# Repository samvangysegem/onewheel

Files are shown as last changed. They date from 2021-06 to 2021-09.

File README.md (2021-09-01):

## OneDuino
&nbsp;
&nbsp;
&nbsp;
&nbsp;
&nbsp;
&nbsp;

### :clipboard: Summary
The goal of this project is to build a one-wheeled robot from scratch. This includes mechanical design of the robot, component selection, electrical design, control system design and embedded programming. The MCU at the hearth of the robot is a Teensy 4.0, packing enough computational power to experiment with optimisation based control strategies. I started this project with two goals in mind: rehearsing a number of important aspects of control theory and the Arduino C/C++ languages and generally improving my embedded programming skills. 

### :construction: Progress
- [x] Model derivation using Euler-Lagrange equations
- [x] 3D design of robot in Solidworks
- [x] Component selection
- [x] LQR control system design
- [x] Circuit design
- [x] 3D printing parts and assembly
- [ ] Coding
- [ ] Countless hours of debugging untill this thing will work

### :computer: Simulation results
This simulation serves as a validation of the correct operation of the LQR controller. The simulation starts with an initial disturbance and ends in a balanced state in x = 1. The LQR control is evidently based on the linearised version of the state-space equations and calculates the optimal input for an infinite optimisation horizon. The simulation on the other hand is the result of numerically integrating the original nonlinear state space equations using a fourth-order Runge-Kutta method.

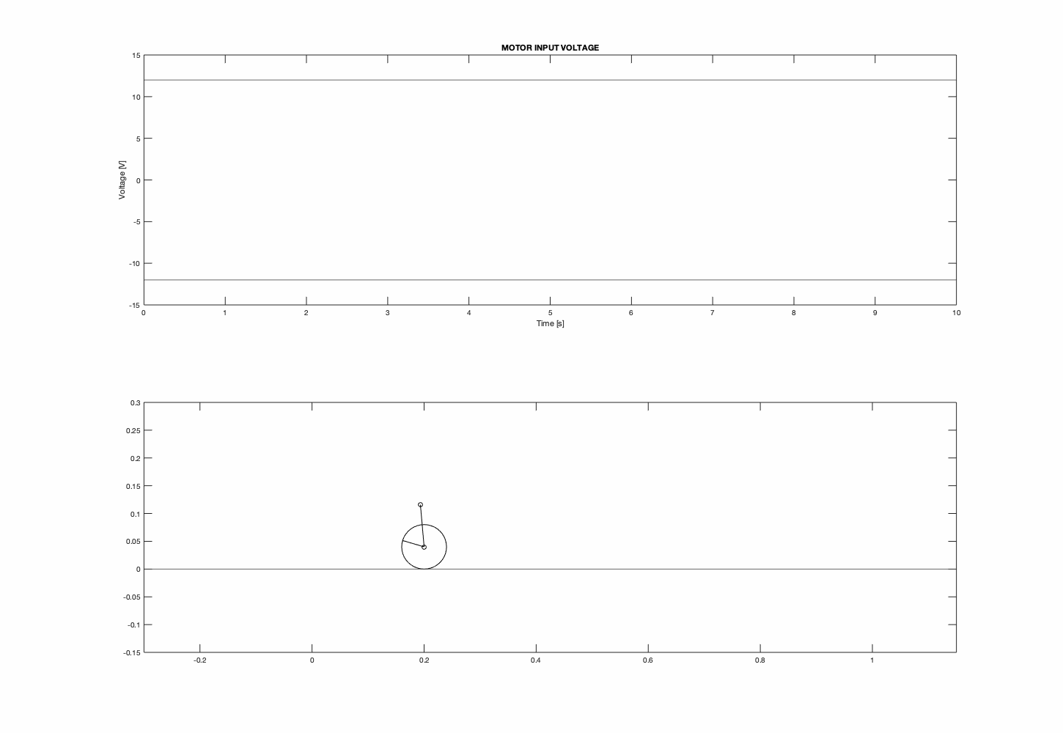
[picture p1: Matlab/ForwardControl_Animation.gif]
Forward LQR Control

 
### :battery: Circuit Design
**Mk1**
The circuit is built on a prototyping PCB given the low complexity of the circuit, which wasn't worth the long waiting time when ordering PCBs online. The board features female headers for connecting the Teensy 4.0 and interfacing with all its pins, 2 male header rows for driving the motors and interfacing with their respective encoders and an MPU6050 module. The red-black wires connect to the Cytron MDD3A dual channel DC motor driver board, in addition to a number of male-female headers for control. As the main focus of this project isn't brushed DC motor control, I didn't bother designing the H-bridges and corresponding driving circuits myself (an idea for an upcoming project, albeit a bit more challenging by replacing the brushed DC motors with brushless DC motors).

| PCB Front | PCB Back |
| --- | --- |
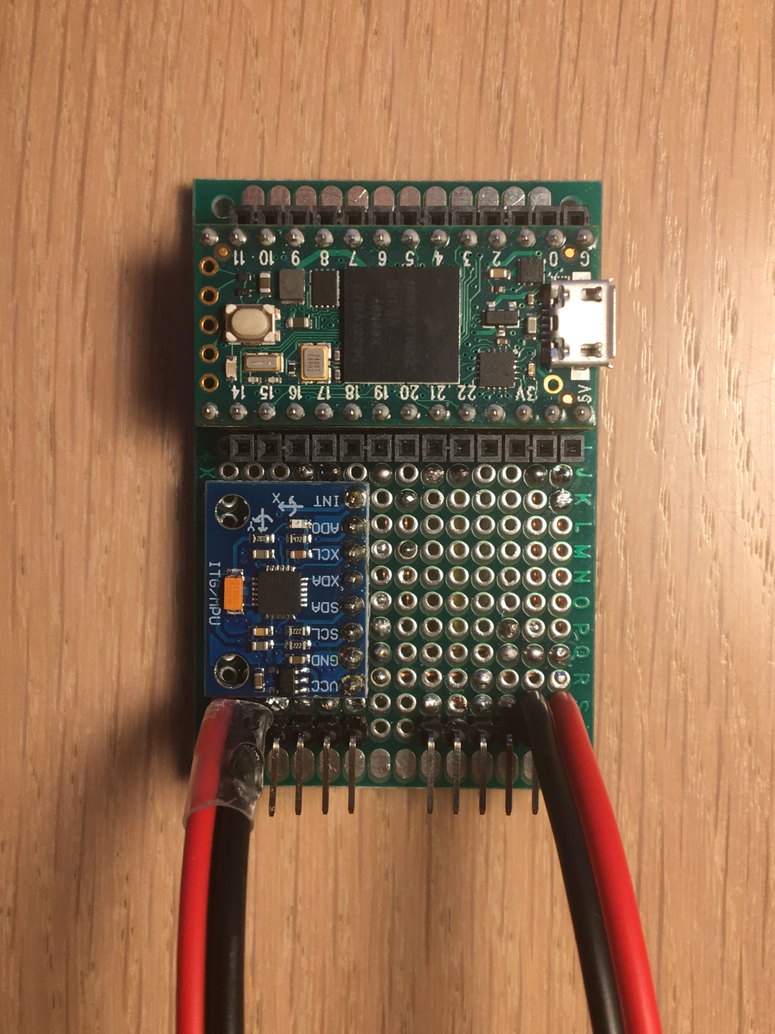
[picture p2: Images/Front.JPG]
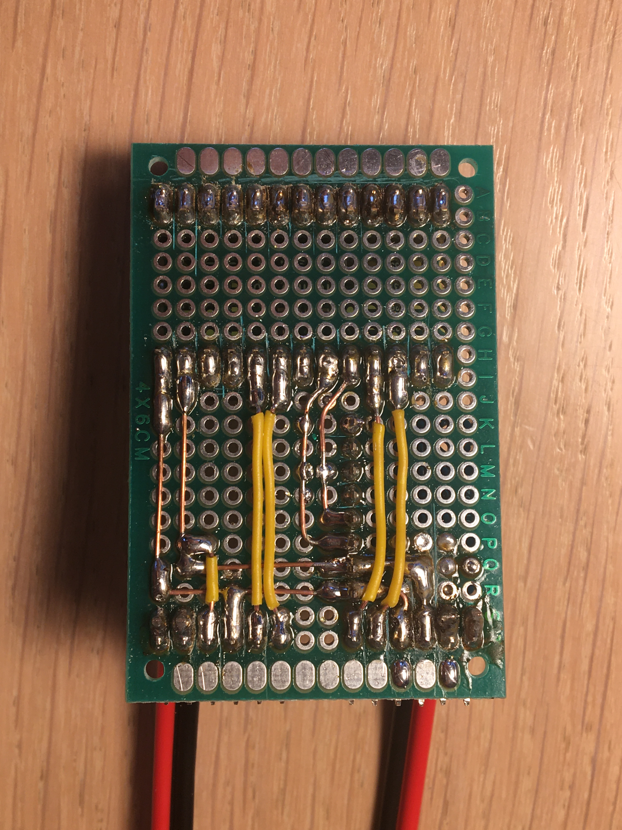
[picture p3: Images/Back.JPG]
 | 

**Mk2**
Since the first design immediately burned down upon testing, as described in the Troubleshooting section below, a second design of the prototyping PCB was made with some changes mitigating the risk of short circuits. The main difference in design is the use of both sides of the prototyping PCB and more careful soldering, not burning the isolation of important wires...

| PCB Front | PCB Back |
| --- | --- |
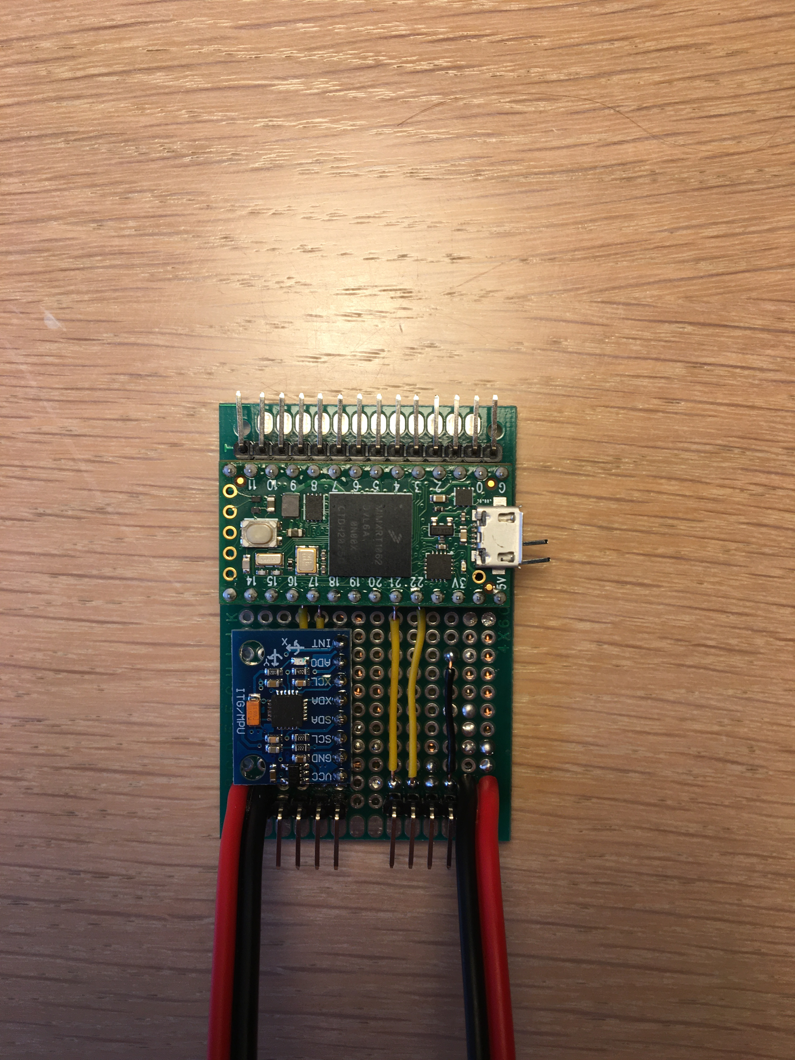
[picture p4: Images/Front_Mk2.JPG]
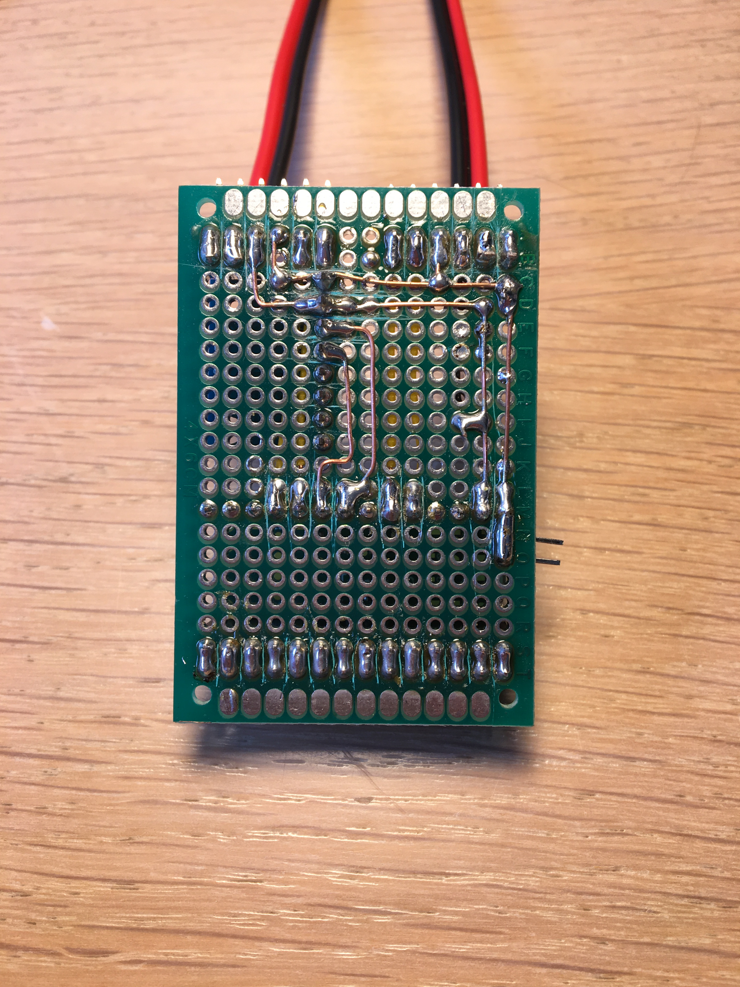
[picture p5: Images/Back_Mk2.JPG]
 | 

### :hammer_and_wrench: Assembly
A few hours of "being creative with incorrect dimensioning of bearing clearances and shaft diameters" later, the full assembly is finished (except for the belt, which is still on its way but we can imagine that part). No short circuits, not falling apart and it looks pretty sweet even if I say so myself...

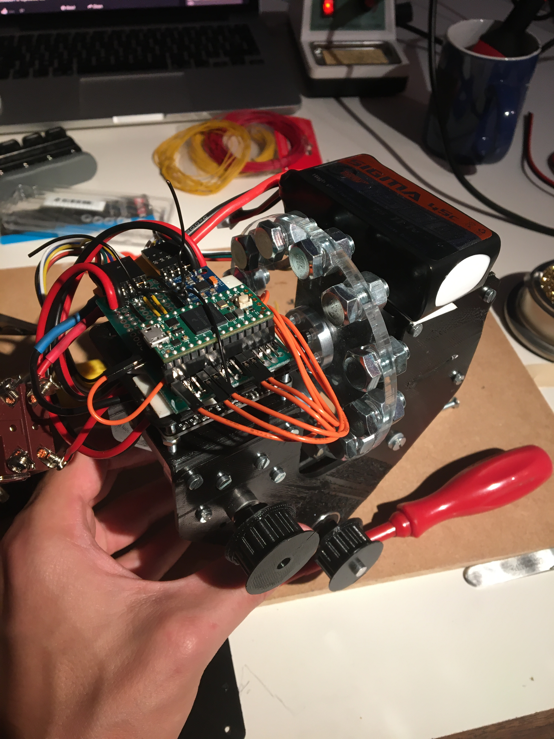
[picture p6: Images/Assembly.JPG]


### :warning: Troubleshooting
- Short circuit occured on the prototyping PCB during a motor test with battery supply. Upon closer inspection, the isolation of one of the motor wires melted during soldering. Solder from a wire next to it entered the isolation through this hole, nearly making contact with the other wire. Even though no short circuit was measured during testing, the higher current required for driving the motor in combination with slight wire movement (possibly) caused a short circuit between these two wires. As a result, a voltage of 12 V was applied to the GND output of the Teensy, resulting in a fried voltage regulator, IMU (also connected to this GND) in addition to internal damage of the Teensy.

    **Conclusion** 
    - When wire isolation melted and unsure whether a short circuit will occur, assume the worst
    - Test motor interfaces first, without Teensy

- LQR control currently is way to aggressive. The robot kinda wants to destroy itself upon receiving power and starting in "balance". There are two ways to address this problem (in my opinion):
    - Improve the model of the balancer
    - Increase the cost of the applied input

    The latter one earns my preference since it requires less rework to the model and code. The influence of these changes will first be verified in simulation before applying it to the actual model.

    **Update** 
    Upon further testing, the problem couldn't be solved as easily as described above. In order to debug this matter in a qualitative manner, following actions are required:
     - Write a python script responsible for visualising and debugging the data sent via the serial interface
     - Design filters for the measured data
     - Debug the Kalman filter class

    Additionally, some library files were added into the project folder itself as I changed some of the parameters of the MPU6050 in those libraries and this was the only way for the Arduino IDE to use the correct libraries.

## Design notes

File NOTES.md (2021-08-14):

## General structure

https://docs.wpilib.org/en/stable/docs/software/commandbased/what-is-command-based.html

## Mechanical Design

### Flywheel Design
3D printed wheel lacks the weight to fulfill the role of a flywheel. Therefore, a number of bolts are added at a large outside diameter to increase the total moment of inertia.

Source: https://itafasteners.com/weight-chart.php
According to the site mentioned above, the total weight of 100 M8 bolts is approximately 1.593kg, resulting in a weight of 15.9g x 12 at a radius of 40mm (with nuts).

Outside diameter: 95mm
Inside diameter: 7mm
Diameter of bols: 80mm
Pitch diameter fastening nuts: 19.06mm
Diameter fastening nuts: 3.4mm

**Components**
* Bolts
    * Online store: https://nl.rs-online.com/web/p/hex-bolts/0190254
* Nuts
    * Online store: https://nl.rs-online.com/web/p/hex-nuts/1224404

### Belt/Pulley Design
Calculator: https://www.bbman.com/belt-length-calculator/

* Center distance
    * 70 mm

**Components**
* Pulleys
    * 16 teeth
    * 25.5 mm pitch diameter
    * 3D Model: https://www.traceparts.com/en/product/gates-standard-pulley-t5-pitch-5-mm-width-10-mm-number-of-teeth-16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

* Belt: 220mm length
    * Online store: https://nl.rs-online.com/web/p/timing-belts/4745347/

## Software Design
Control is split up in forwards and sideways control, assuming independent systems (which off course is not correct but for sufficiently small deviations should provide a good approach to control). 

### MPU6050
Calibration is required to guarantee correct operating behaviour. This can be achieved through the MPU 6050 library in the Arduino IDE, example sketch "IMU_Zero.ino". Calibration is best performed before installing the sensor on the robot in order to yield optimal results on a flat surface.

General operation: https://mjwhite8119.github.io/Robots/mpu6050

### Motor Encoders

### Kalman Filter
The Kalman filter is responsible for estimating the necessary velocity estimates based on the position estimates and mathematical model. Immediately deriving the velocity from the position estimate would induces a high amount of noise in the velocity estimates. Integrating the acceleration values on the other hand would be another good approach, however these are quite difficult to access.

### LQR Control

### Matrix4 and Vector4
Custom classes written to perform matrix calculations for Kalman filter and LQR control. Row and column vectors are separated in order to easily implement the multiplication overloading of these different vectors with each other and matrices.
- [ ] Inverse operator for Matrix class (efficient implementation)
- [ ] Copy constructors

## Git Commands
git status
git log --stat
git add
git commit -m "Message"
git push
git pull
git rm --cached *filename*

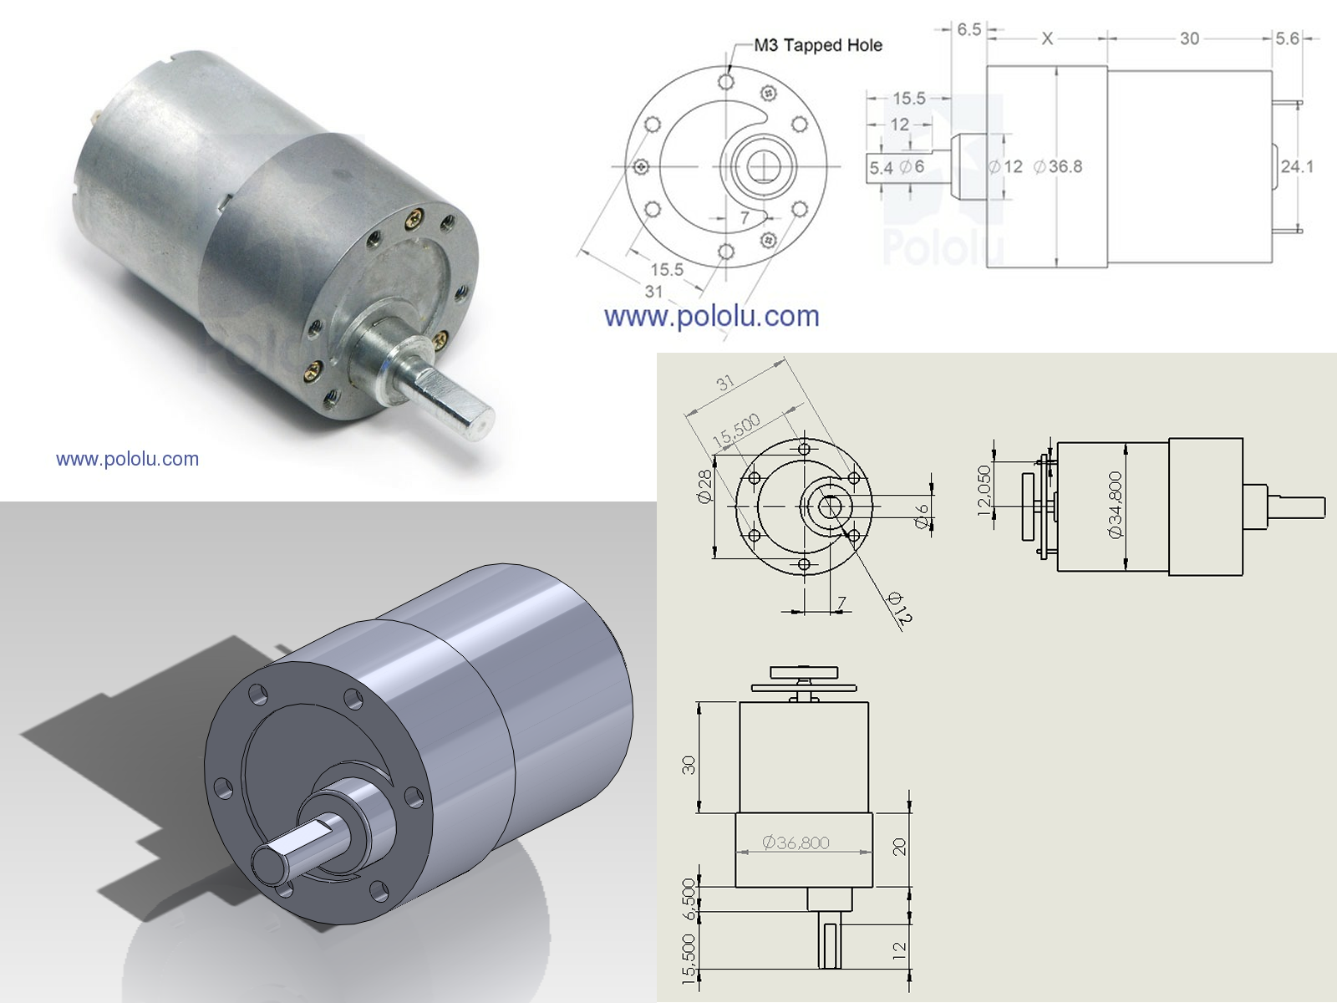
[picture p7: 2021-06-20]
Solidworks/pololu-37dx52l-mm-with-64-cpr-encoder/Renderings/pololu-37D-encoder.png

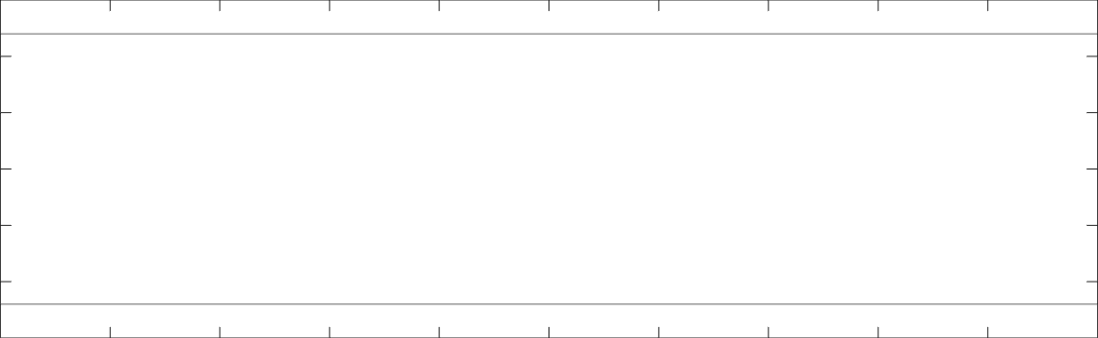
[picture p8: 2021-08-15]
Matlab/ForwardControl_Control.gif

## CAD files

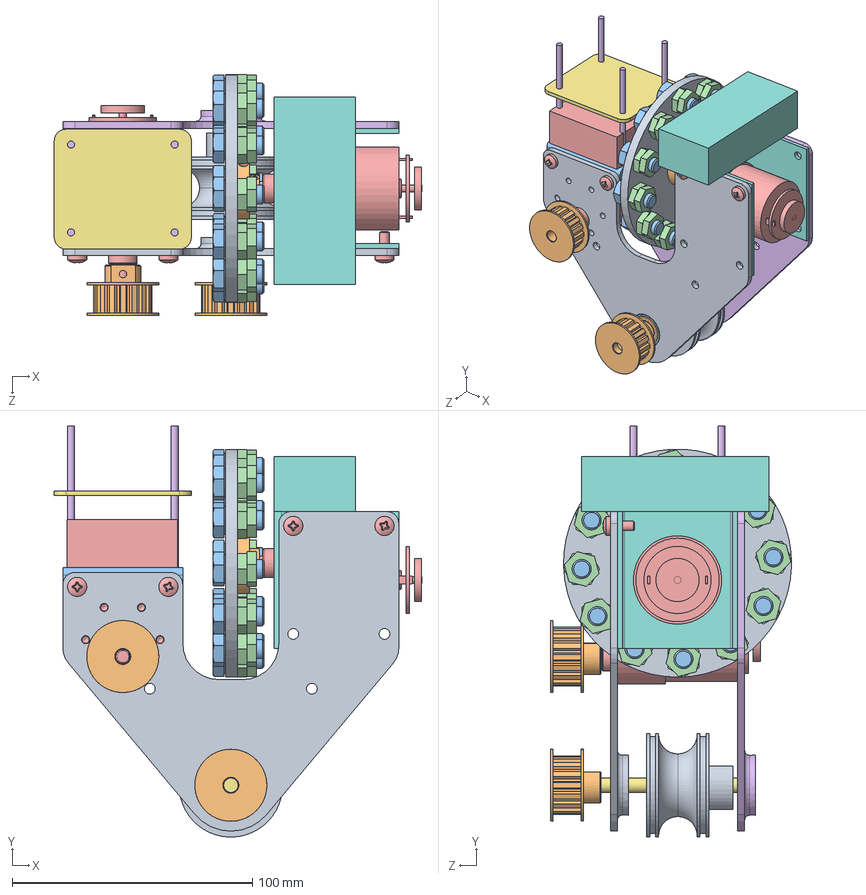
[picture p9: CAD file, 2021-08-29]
Solidworks/OneWheel.SLDASM
153.1 x 171.2 x 100.4 mm
ZijplaatL
_626_2Z_PART1_2 x 2
_626_2Z_PART2_4 x 2
_626_2Z_PART3_6 x 16
pololu-37D-encoder x 2
ZijplaatR
Wheelaxis
Motorhouder
Vliegwiel
Wheel Hub
Elechouder
NUTM4 x 2
din_en_iso7045_m4x10_4_8h x 4
Elecsupportbeam x 4
Elecmount
Battery
Velg
T5Pulley2 x 2
screw_din_933-m8x16-10_9-a x 12
fath_4din439bm8e x 24
Contra

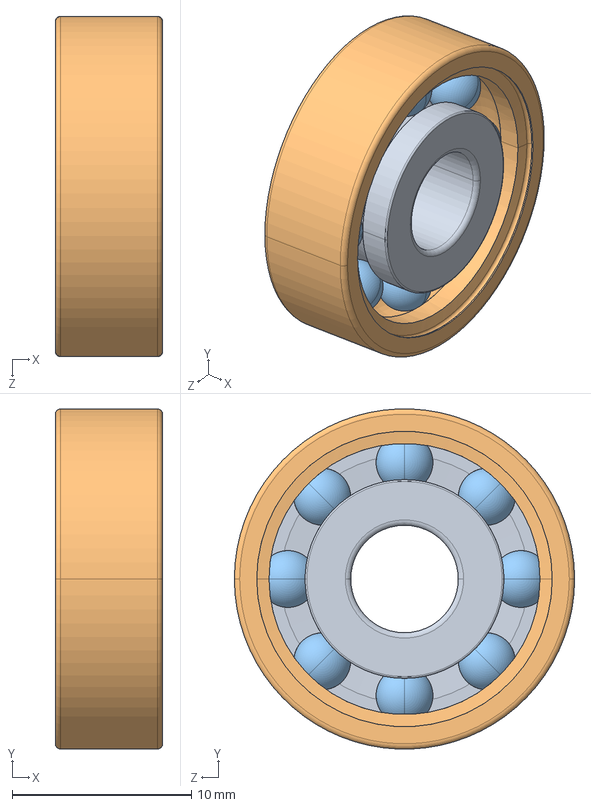
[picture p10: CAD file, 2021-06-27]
Solidworks/626_2Z.sldasm
6.00 x 19.0 x 19.0 mm
_626_2Z_PART1_2
_626_2Z_PART2_4
_626_2Z_PART3_6 x 8

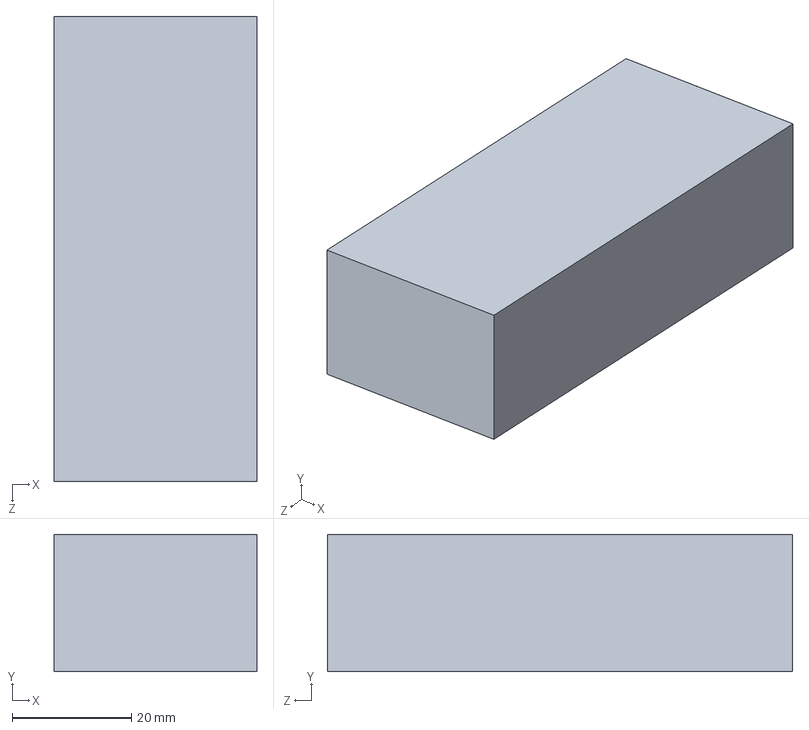
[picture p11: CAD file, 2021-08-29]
Solidworks/Battery.SLDPRT
34.0 x 23.0 x 78.0 mm

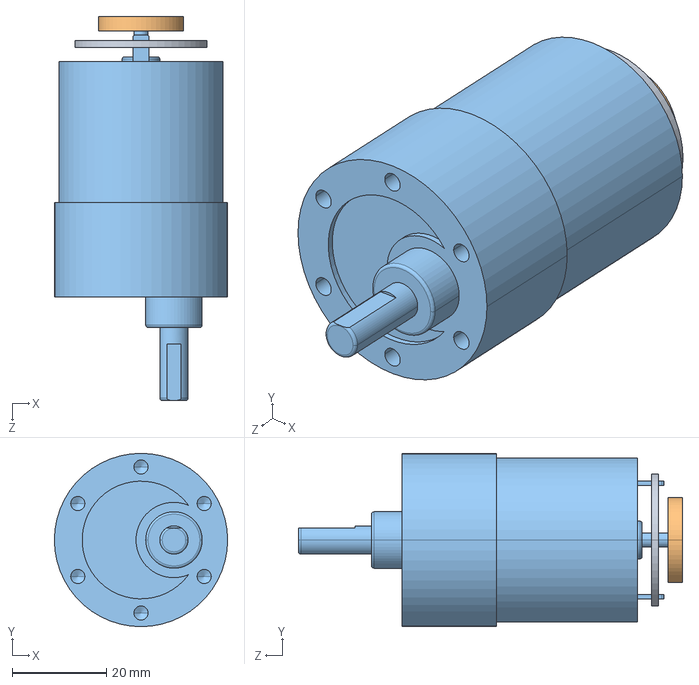
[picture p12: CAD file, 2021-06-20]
Solidworks/pololu-37dx52l-mm-with-64-cpr-encoder/pololu-37D-encoder.STEP
36.8 x 36.8 x 81.5 mm

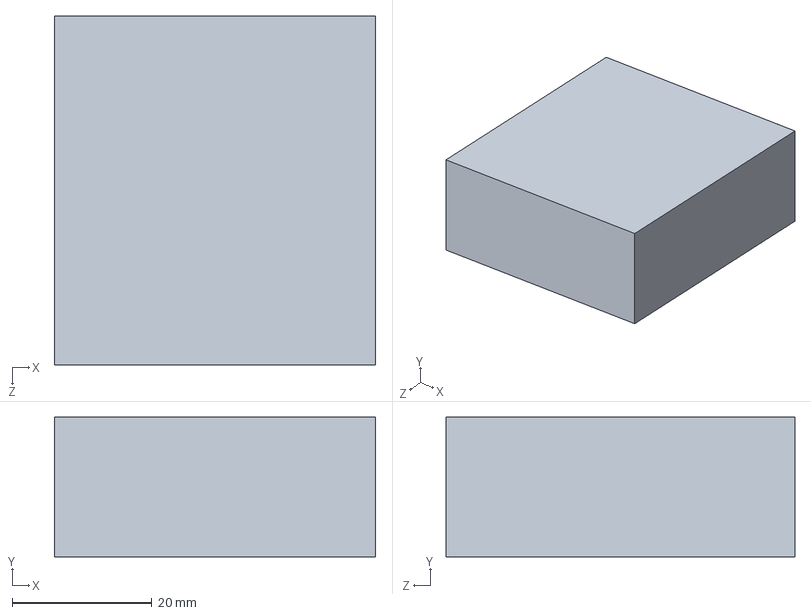
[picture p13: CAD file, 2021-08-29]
Solidworks/Contra.SLDPRT
46.0 x 20.0 x 50.0 mm

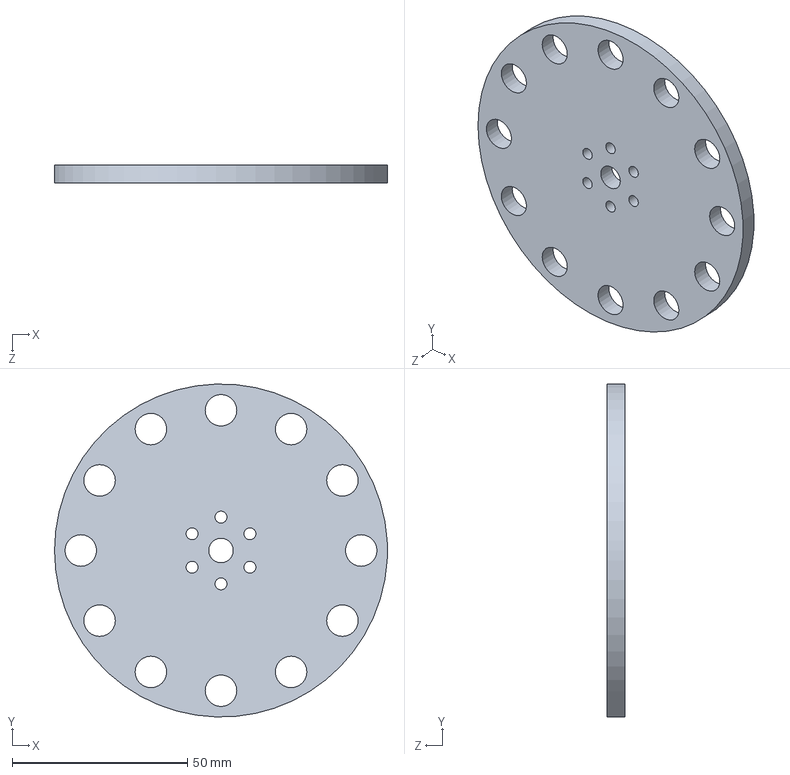
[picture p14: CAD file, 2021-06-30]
Solidworks/Vliegwiel.SLDPRT
95.0 x 95.0 x 5.00 mm

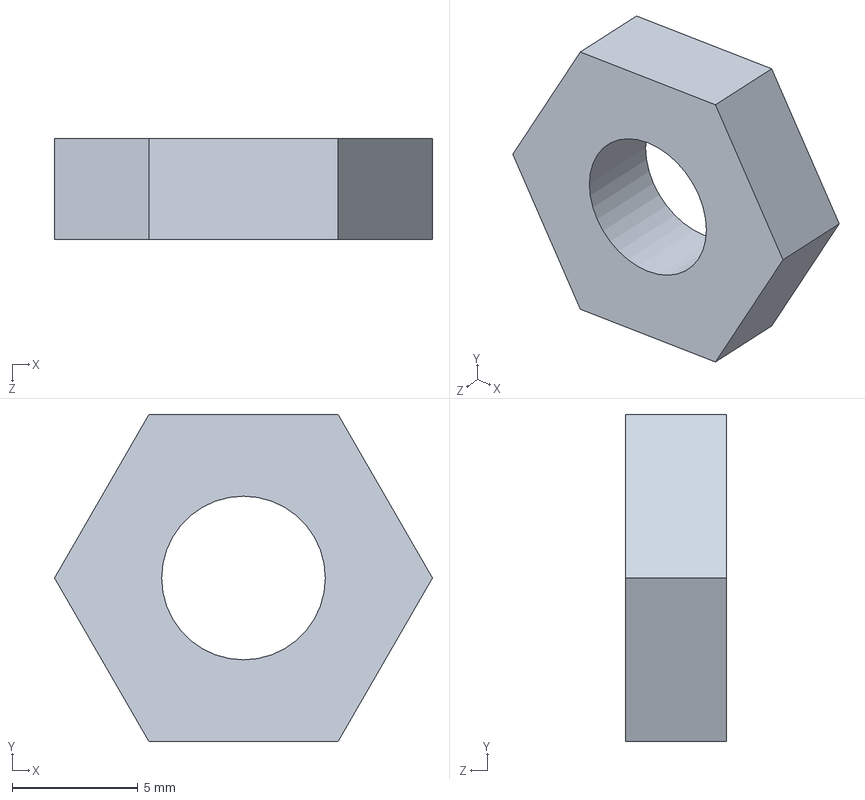
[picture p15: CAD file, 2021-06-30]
Solidworks/fath_4din439bm8e.SLDPRT
15.0 x 13.0 x 4.00 mm

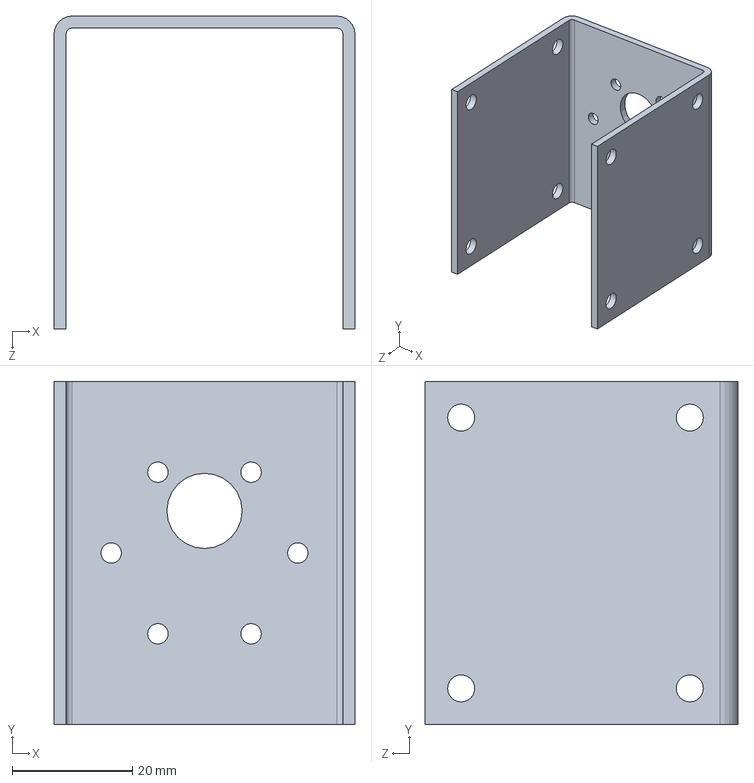
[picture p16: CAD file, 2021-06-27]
Solidworks/Motorhouder.SLDPRT
50.0 x 57.0 x 52.0 mm

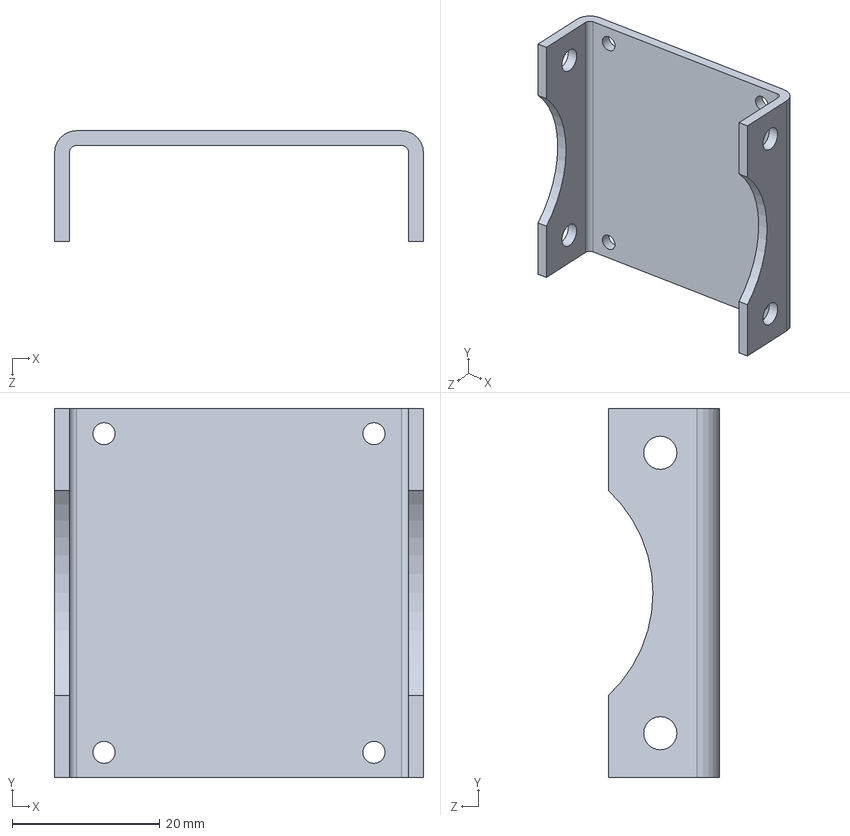
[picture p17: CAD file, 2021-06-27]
Solidworks/Elechouder.SLDPRT
50.0 x 50.0 x 15.0 mm

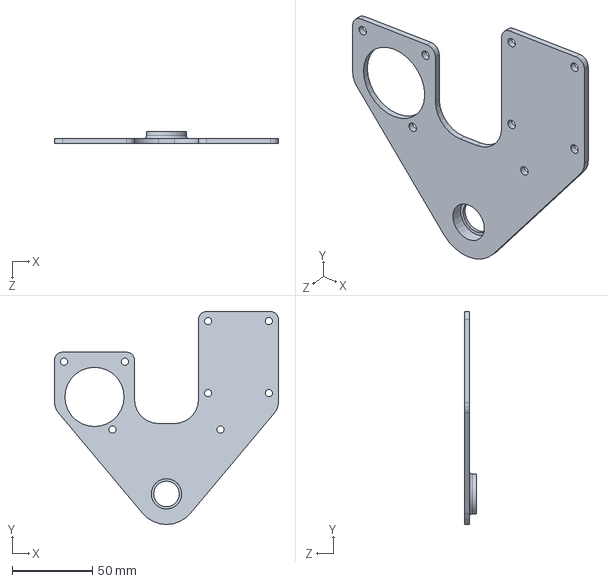
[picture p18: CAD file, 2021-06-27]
Solidworks/ZijplaatR.SLDPRT
140.0 x 133.1 x 7.50 mm

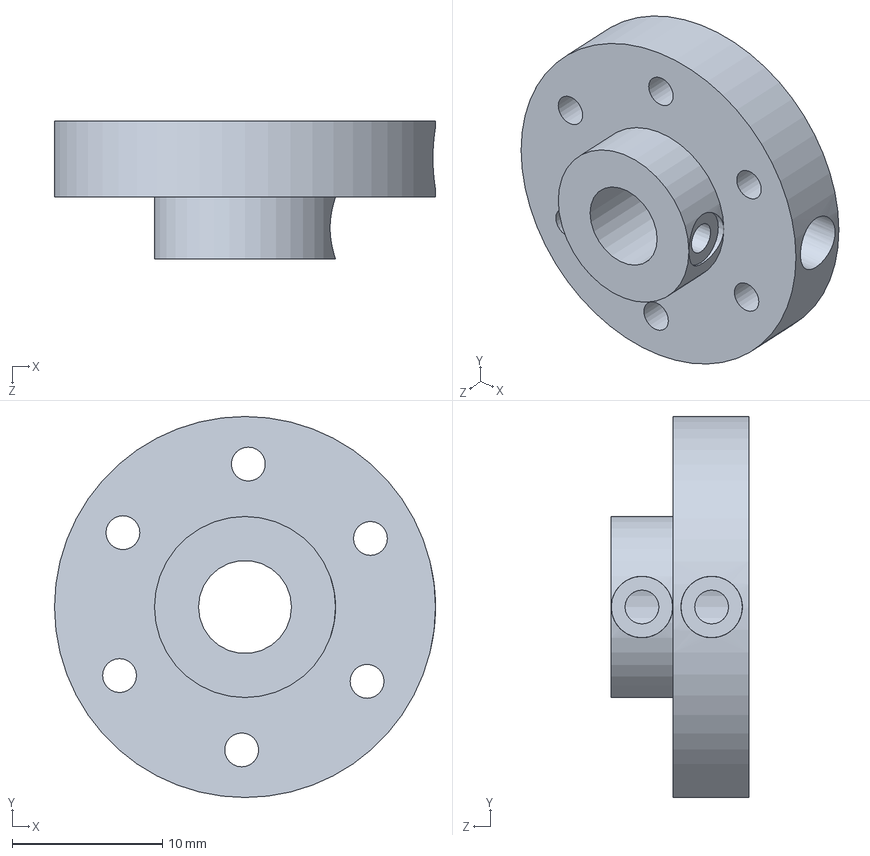
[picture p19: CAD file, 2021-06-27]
Solidworks/Wheel Hub.SLDPRT
25.4 x 25.4 x 9.21 mm

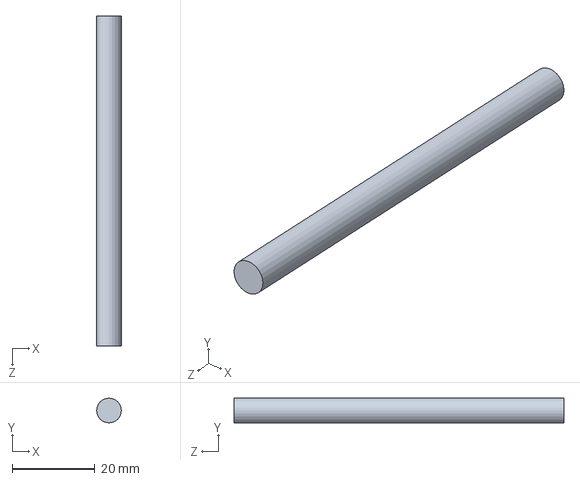
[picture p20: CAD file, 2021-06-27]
Solidworks/Wheelaxis.SLDPRT
6.00 x 6.00 x 80.0 mm

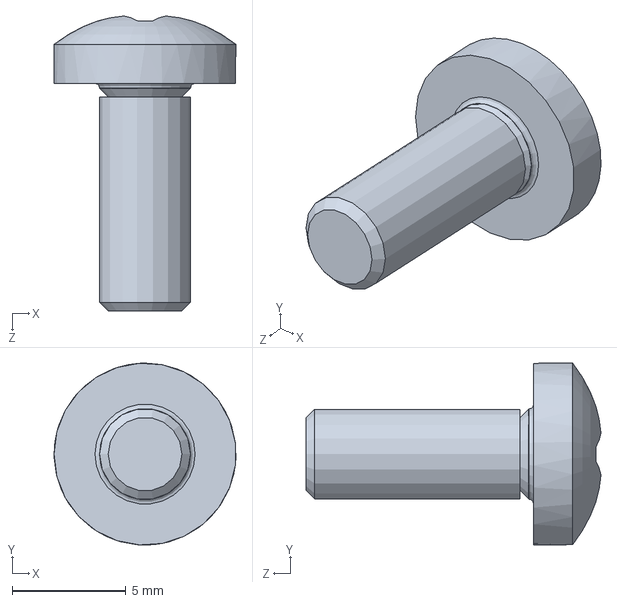
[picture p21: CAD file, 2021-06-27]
Solidworks/din_en_iso7045_m4x10_4_8h.SLDPRT
8.00 x 7.99 x 13.0 mm

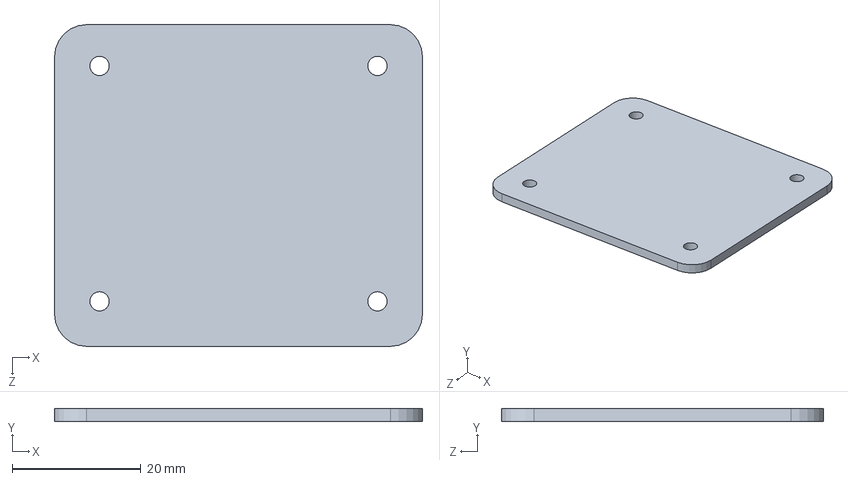
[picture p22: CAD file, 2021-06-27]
Solidworks/Elecmount.SLDPRT
57.2 x 2.00 x 50.0 mm

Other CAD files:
Solidworks/_626_2Z_PART3_6.sldprt
Solidworks/_626_2Z_PART2_4.sldprt
Solidworks/ZijplaatL.SLDPRT
Solidworks/NUTM4.SLDPRT
Solidworks/Elecsupportbeam.SLDPRT
Solidworks/MLXPulley.SLDPRT
Solidworks/PanHeadCrossRecessedScrew_M4x12.STEP
Solidworks/T5Pulley.SLDPRT
Solidworks/T5Pulley2.SLDPRT
Solidworks/Velg.SLDPRT
Solidworks/_626_2Z_PART1_2.sldprt
Solidworks/din_en_iso7045_m4x14_4_8h.SLDPRT
Solidworks/pololu-37dx52l-mm-with-64-cpr-encoder/pololu-37D-encoder.SLDDRW
Solidworks/pololu-37dx52l-mm-with-64-cpr-encoder/pololu-37D-encoder.SLDPRT
Solidworks/pololu-37dx52l-mm-with-64-cpr-encoder/pololu-37D-encoder.STL
Solidworks/screw_din_933-m8x16-10_9-a.SLDPRT

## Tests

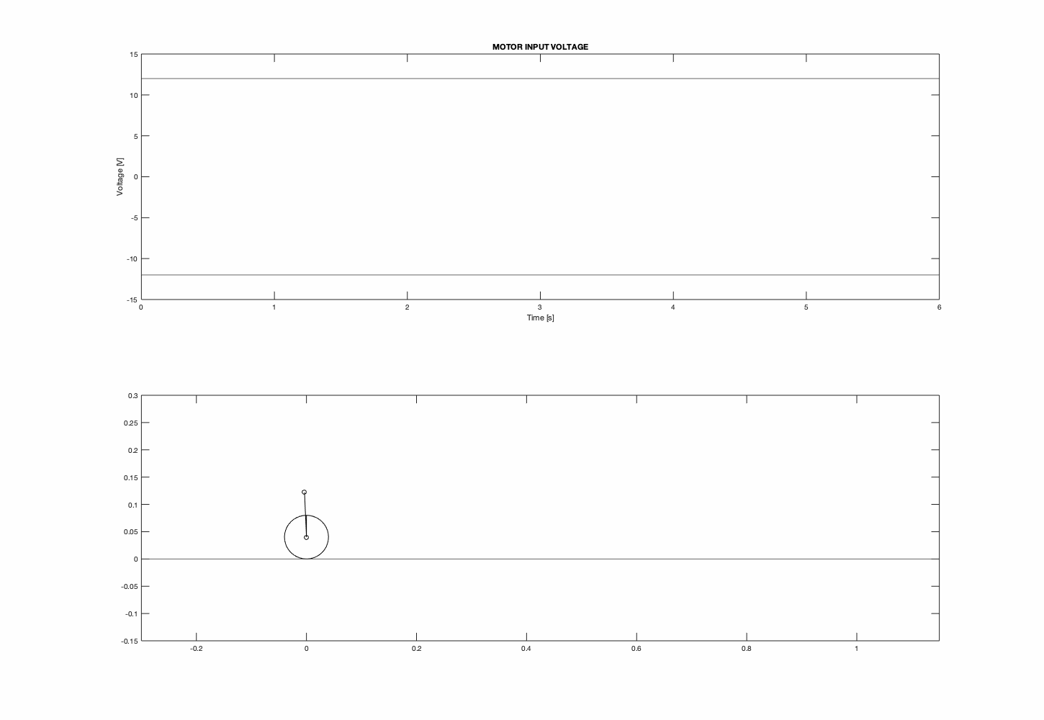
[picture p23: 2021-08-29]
Matlab/TEST.gif

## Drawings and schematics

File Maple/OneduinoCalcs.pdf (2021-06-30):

## Dynamics Forward/Backwards

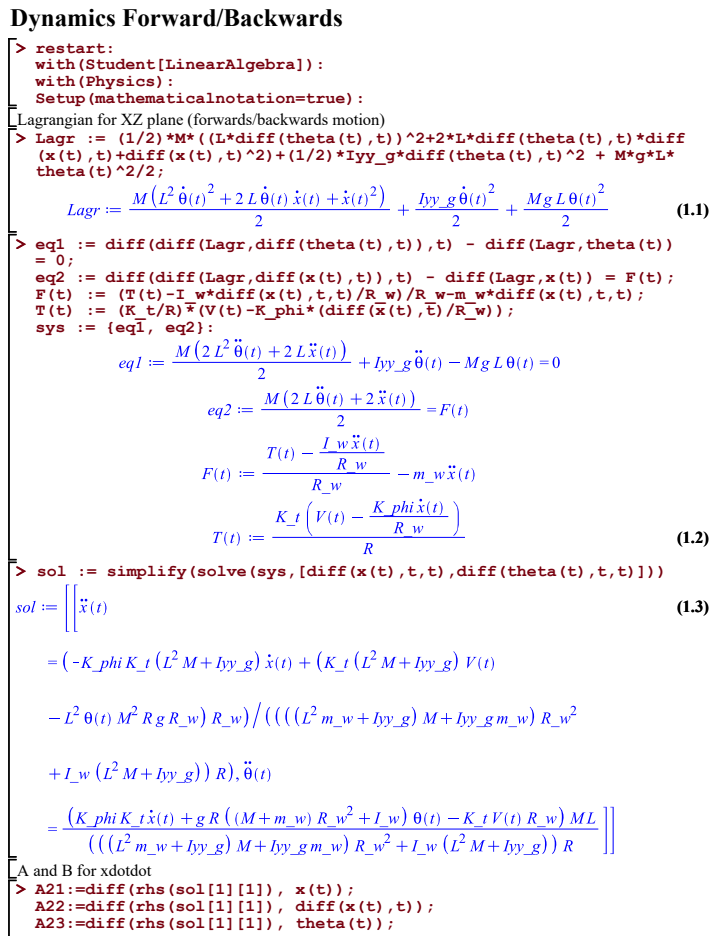
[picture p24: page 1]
restart:

with(Student[LinearAlgebra]):
with(Physics):
Setup(mathematicalnotation=true):
Lagrangian for XZ plane (forwards/backwards motion)
Lagr := (1/2)*M*((L*diff(theta(t),t))^2+2*L*diff(theta(t),t)*diff
(x(t),t)+diff(x(t),t)^2)+(1/2)*Iyy_g*diff(theta(t),t)^2 + M*g*L*
theta(t)^2/2;

eq1 := diff(diff(Lagr,diff(theta(t),t)),t) - diff(Lagr,theta(t))
eq2 := diff(diff(Lagr,diff(x(t),t)),t) - diff(Lagr,x(t)) = F(t);
F(t) := (T(t)-I_w*diff(x(t),t,t)/R_w)/R_w-m_w*diff(x(t),t,t);
T(t) := (K_t/R)*(V(t)-K_phi*(diff(x(t),t)/R_w));
sys := {eq1, eq2}:

sol := simplify(solve(sys,[diff(x(t),t,t),diff(theta(t),t,t)]))

A and B for xdotdot
A21:=diff(rhs(sol[1][1]), x(t));
A22:=diff(rhs(sol[1][1]), diff(x(t),t));
A23:=diff(rhs(sol[1][1]), theta(t));

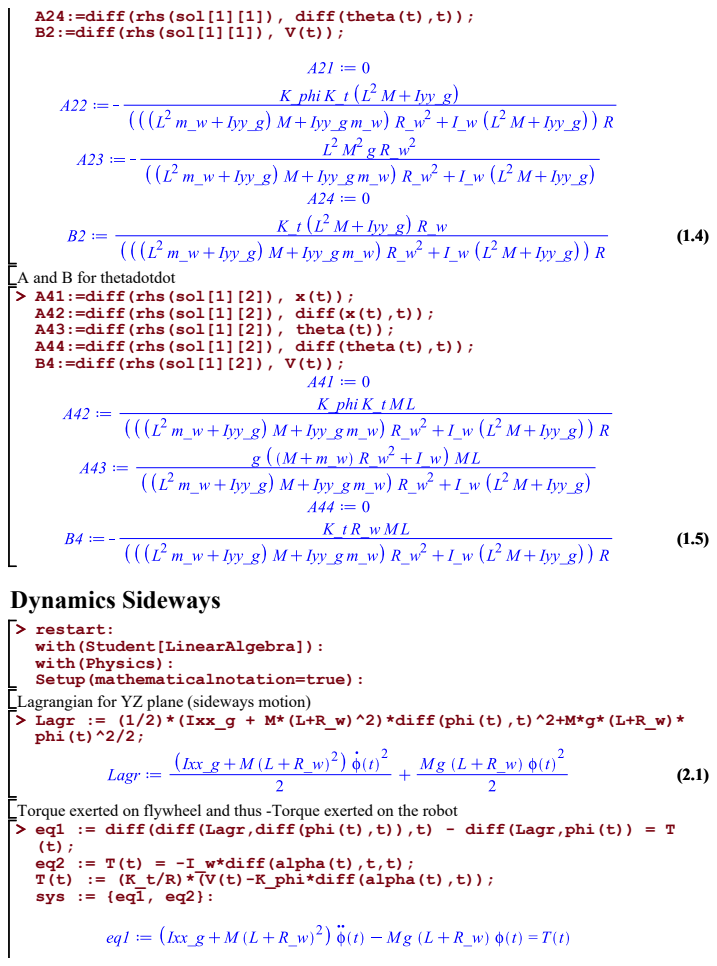
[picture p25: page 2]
Dynamics Sideways; restart:

A24:=diff(rhs(sol[1][1]), diff(theta(t),t));
B2:=diff(rhs(sol[1][1]), V(t));

A and B for thetadotdot
A41:=diff(rhs(sol[1][2]), x(t));
A42:=diff(rhs(sol[1][2]), diff(x(t),t));
A43:=diff(rhs(sol[1][2]), theta(t));
A44:=diff(rhs(sol[1][2]), diff(theta(t),t));
B4:=diff(rhs(sol[1][2]), V(t));

with(Student[LinearAlgebra]):
with(Physics):
Setup(mathematicalnotation=true):
Lagrangian for YZ plane (sideways motion)
Lagr := (1/2)*(Ixx_g + M*(L+R_w)^2)*diff(phi(t),t)^2+M*g*(L+R_w)*
phi(t)^2/2;

Torque exerted on flywheel and thus -Torque exerted on the robot
eq1 := diff(diff(Lagr,diff(phi(t),t)),t) - diff(Lagr,phi(t)) = T
eq2 := T(t) = -I_w*diff(alpha(t),t,t);
T(t) := (K_t/R)*(V(t)-K_phi*diff(alpha(t),t));
sys := {eq1, eq2}:

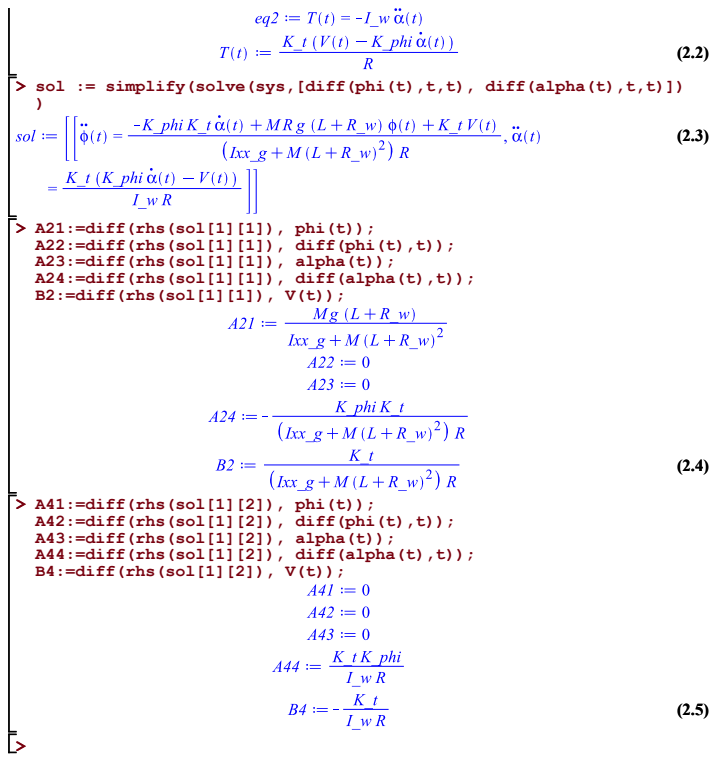
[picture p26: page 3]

sol := simplify(solve(sys,[diff(phi(t),t,t), diff(alpha(t),t,t)])

A21:=diff(rhs(sol[1][1]), phi(t));
A22:=diff(rhs(sol[1][1]), diff(phi(t),t));
A23:=diff(rhs(sol[1][1]), alpha(t));
A24:=diff(rhs(sol[1][1]), diff(alpha(t),t));
B2:=diff(rhs(sol[1][1]), V(t));

A41:=diff(rhs(sol[1][2]), phi(t));
A42:=diff(rhs(sol[1][2]), diff(phi(t),t));
A43:=diff(rhs(sol[1][2]), alpha(t));
A44:=diff(rhs(sol[1][2]), diff(alpha(t),t));
B4:=diff(rhs(sol[1][2]), V(t));

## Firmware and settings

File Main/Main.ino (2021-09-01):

// ================================================================
// ===                         ONEDUINO                         ===
// ================================================================

// https://forum.arduino.cc/index.php?topic=408980.0 Post nr 4

#define DEBUG
#define __ASSERT_USE_STDERR //NDEBUG in the case of leaving out asserts

#ifdef DEBUG
#define DPRINTSTIMER(t)    for (static unsigned long SpamTimer; (unsigned long)(millis() - SpamTimer) >= (t); SpamTimer = millis())
#define DPRINTSFN(StrSize,Name,...) {char S[StrSize];Serial.print("\t");Serial.print(Name);Serial.print(" "); Serial.print(dtostrf((float)__VA_ARGS__ ,S));} //StringSize,Name,Variable,Spaces,Percision
#define DPRINTLN(...)      Serial.println(__VA_ARGS__)
#define DEBUGMODE          true
#else
#define DPRINTSTIMER(t)    if(false)
#define DPRINTSFN(...)     //blank line
#define DPRINTLN(...)      //blank line
#define DEBUGMODE          false
#endif

#define sgn(x) ((x) < 0 ? -1 : 1)
#define CONTROL_FREQUENCY 10 // Hz

// ================================================================
// ===                        LIBRARIES                         ===
// ================================================================

// Installed libraries
#include <assert.h>
#include <Wire.h>
#include <Encoder.h>

// Custom libraries
#include "I2Cdev.h"
#include "MPU6050_6Axis_MotionApps20.h"
#include "Kalman.h"
#include "LQR.h"

#define LED_PIN 13

#define M1A 7
#define M1B 8

#define M2A 2
#define M2B 3

// ================================================================
// ===                      I2C SETUP Items                     ===
// ================================================================
void i2cSetup() {
  // join I2C bus (I2Cdev library doesn't do this automatically)
  #if I2CDEV_IMPLEMENTATION == I2CDEV_ARDUINO_WIRE
    Wire.begin();
    Wire.setClock(400000); // 400kHz I2C clock (200kHz if CPU is 8MHz)
  #elif I2CDEV_IMPLEMENTATION == I2CDEV_BUILTIN_FASTWIRE
    Fastwire::setup(400, true);
  #endif
}

// ================================================================
// ===                  CONTROL LOOP INTERRUPT                  ===
// ================================================================
// Up to 4 intervaltimers can run simultaneously. They trigger the
// associated interrupts methods at a fixed frequency.
volatile bool controlInterrupt = false;

void controlInterruptHandler() {
  controlInterrupt = true;
}

IntervalTimer controlTimer;

void timersSetup() {
  controlTimer.priority(1);
  controlTimer.begin(controlInterruptHandler, 1000000/CONTROL_FREQUENCY); // Expressed in microseconds
}

// ================================================================
// ===                      MPU DMP SETUP                       ===
// ================================================================
MPU6050 mpu;

int FifoAlive = 0;     // tests if the interrupt is triggering
int IsAlive = -20;     // counts interrupt start at -20 to get 20+ good values before assuming connected

// MPU control/status vars
uint8_t mpuIntStatus;   // holds actual interrupt status byte from MPU
uint8_t devStatus;      // return status after each device operation (0 = success, !0 = error)
uint16_t packetSize;    // expected DMP packet size (default is 42 bytes)
uint16_t fifoCount;     // count of all bytes currently in FIFO
uint8_t fifoBuffer[64]; // FIFO storage buffer

// Orientation/motion vars
Quaternion q;           // [w, x, y, z]         quaternion container
VectorInt16 aa;         // [x, y, z]            accel sensor measurements
VectorInt16 aaReal;     // [x, y, z]            gravity-free accel sensor measurements
VectorInt16 aaWorld;    // [x, y, z]            world-frame accel sensor measurements
VectorFloat gravity;    // [x, y, z]            gravity vector
VectorInt16 gyro;       // [x, y, z]            rotational velocities around all three axes

float euler[3];         // [psi, theta, phi]    Euler angle container
float ypr[3];           // [yaw, pitch, roll]   yaw/pitch/roll container and gravity vector
byte StartUP = 100;     // lets get 100 readings from the MPU before we start trusting them

int MPUOffsets[6] = {-8423, -565, 1008, 58, -38, 64};

void MPU6050Connect() {
  static int MPUInitCntr = 0; // Static: not deleted when function ends which allows values to be reused in subsequent function calls
  // Initialize device
  mpu.initialize();
  // Load and configure the DMP
  devStatus = mpu.dmpInitialize();

  if (devStatus != 0) {
    // ERROR!
    // 1 = initial memory load failed
    // 2 = DMP configuration updates failed
    // (if it's going to break, usually the code will be 1)

    const char* StatStr[5] { "No Error", "Initial memory load failed", "DMP configuration updates failed", "3", "4"};

    MPUInitCntr++;

    Serial.print(F("MPU connection Try #"));
    Serial.println(MPUInitCntr);
    Serial.print(F("DMP Initialization failed (code "));
    Serial.print(StatStr[devStatus]);
    Serial.println(F(")"));

    if (MPUInitCntr >= 10) return; //only try 10 times (works because static)
    delay(1000);
    MPU6050Connect(); // Lets try again
    return;
  }
  
  // Assign offsets
  mpu.setXAccelOffset(MPUOffsets[0]);
  mpu.setYAccelOffset(MPUOffsets[1]);
  mpu.setZAccelOffset(MPUOffsets[2]);
  mpu.setXGyroOffset(MPUOffsets[3]);
  mpu.setYGyroOffset(MPUOffsets[4]);
  mpu.setZGyroOffset(MPUOffsets[5]);
  
  // No calibration is required since this has been done beforehand
  //mpu.CalibrateAccel(6);
  //mpu.CalibrateGyro(6);
  //mpu.PrintActiveOffsets();
  Serial.println(F("Enabling DMP..."));
  mpu.setDMPEnabled(true);
  packetSize = mpu.dmpGetFIFOPacketSize();
  delay(1000); // Let it Stabelize
  mpu.resetFIFO(); // Clear fifo buffer
}

// ================================================================
// ===                    MPU DMP Get Data                      ===
// ================================================================
void GetDMP() { 
  // Best version I have made so far
  // Serial.println(F("FIFO interrupt at:"));
  // Serial.println(micros());
  // static unsigned long LastGoodPacketTime;
  // mpuInterrupt = false;
  FifoAlive = 1;
  fifoCount = mpu.getFIFOCount();
  if ((!fifoCount) || (fifoCount % packetSize)) { // we have failed Reset and wait till next time!
    // digitalWrite(LED_PIN, LOW); // lets turn off the blinking light so we can see we are failing.
    mpu.resetFIFO();// clear the buffer and start over
  } else {
    while (fifoCount  >= packetSize) { // Get the packets until we have the latest!
      mpu.getFIFOBytes(fifoBuffer, packetSize); // lets do the magic and get the data
      fifoCount -= packetSize;
    }
    // LastGoodPacketTime = millis();
    MPUMath(); // <<<<<<<<<<<<<<<<<<<<<<<<<<<< On success MPUMath() <<<<<<<<<<<<<<<<<<<
    // digitalWrite(LED_PIN, !digitalRead(LED_PIN)); // Blink the Light
  }
}

// ================================================================
// ===                    MPU Polling Data                      ===
// ================================================================
// Alternative to GetDMP without use of interrupts

float Yaw, Pitch, Roll;
float YawVel, PitchVel, RollVel;

void pollDMP() {
  // Clear MPU value in order to get latest value
  mpu.resetFIFO();
  // Get current FIFO count
  fifoCount = mpu.getFIFOCount();
  // wait for correct available data length, should be a VERY short wait
  while (fifoCount < packetSize) fifoCount = mpu.getFIFOCount();
  // Read a packet from FIFO
  mpu.getFIFOBytes(fifoBuffer, packetSize);
  // Further calculations
  MPUMath();
}

// ================================================================
// ===                        MPU Math                          ===
// ================================================================

void MPUMath() {
  mpu.dmpGetGyro(&gyro, fifoBuffer);
  mpu.dmpGetQuaternion(&q, fifoBuffer);
  mpu.dmpGetGravity(&gravity, &q);
  mpu.dmpGetYawPitchRoll(ypr, &q, &gravity);

  YawVel = gyro.z / 32768.0 * 1000.0 * DEG_TO_RAD;
  PitchVel = gyro.y / 32768.0 * 1000.0  * DEG_TO_RAD;
  RollVel = gyro.x / 32768.0 * 1000.0  * DEG_TO_RAD;
  
  Yaw = ypr[0]; // Z
  Pitch = ypr[1]; // Y
  Roll = ypr[2]; // X
}

// ================================================================
// ===                      Encoder METHODS                     ===
// ================================================================

// Encoder for wheel rotation
Encoder wheelEnc(21, 22);
float wheelEncPos, wheelEncVel;

// Encoder for flywheel rotation
Encoder flyEnc(16, 17);
float flyEncPos, flyEncVel;

void encoderSetup() {
  // Both encoder position can be initialised as 0
  // The initial position of the flywheel is of no importance
  // The initial position of the wheel is 0 at startup and thus also of no importance
  wheelEnc.write(0);
  flyEnc.write(0);
}

void pollEncoders() {
  // Get position information
  float oldWheelEncPos = wheelEncPos;
  wheelEncPos = wheelEnc.read() / (18.75 * 64.0) * 2 * PI;
  wheelEncVel = CONTROL_FREQUENCY * (wheelEncPos - oldWheelEncPos);
  float oldFlyEncPos = flyEncPos;
  flyEncPos = flyEnc.read() / (18.75 * 64.0) * 2 * PI;
  flyEncVel = CONTROL_FREQUENCY * (flyEncPos - oldFlyEncPos);
}

// ================================================================
// ===                       Motor METHODS                      ===
// ================================================================

// Source: https://www.pjrc.com/teensy/td_pulse.html#frequency
// Pins M1A = 8 and M1B = 7 are controlled by FlexPWM1.3 timer
// Pins M2A = 3 and M2B = 2 are controlled by FlexPWM4.2 timer
void motorSetup() { 
  // Check if pins still correct, otherwise setup will fail
  assert((M1A == 7) && (M1B == 8));
  assert((M2A == 2) && (M2B == 3));
  // Setup pins as output pins
  pinMode(M1A, OUTPUT);
  pinMode(M1B, OUTPUT);
  pinMode(M2A, OUTPUT);
  pinMode(M2B, OUTPUT);
  // Setup PWM resolution
  analogWriteResolution(12);
  // Now use: analogWrite(port, 0 - 4095)
  // Ideal frequency: 36621.09 Hz
  analogWriteFrequency(M1A, 36621.09); // M1B frequency changes as well
  analogWriteFrequency(M2A, 36621.09); // M2B frequency changes as well
}

void driveMotor(float input, uint8_t portA, uint8_t portB) {
  // Quick action for input 0
  if (input == 0.0){
    analogWrite(portA, 0);
    analogWrite(portB, 0);
    return;
  }
  // Sign and Map to new range
  int8_t signInput = sgn(constrainedInput);
  uint16_t pwmInput = abs(constrainedInput) * 4095 / 12; // Automatically floored to int
  // Write output for motor
  analogWrite((signInput == 1) ? portB : portA, 0); // In case 0 isn't perfectly crossed, turn off other PWM signal
  analogWrite((signInput == 1) ? portA : portB, pwmInput);
  DPRINTSFN(10, " PWM:", pwmInput/4095.0, -6, 2);
  DPRINTLN();
}

void testMotors() {
  // Drive forwards and backwards at different speeds
  driveMotor(1, M1A, M1B); 
  delay(250);
  driveMotor(-1, M1A, M1B);
  delay(250);
  driveMotor(0, M1A, M1B);
  delay(250);
  driveMotor(1, M2A, M2B);
  delay(250);
  driveMotor(-1, M2A, M2B);
  delay(250);
  driveMotor(0, M2A, M2B);
}

// ================================================================
// ===                       Model SETUP                        ===
// ================================================================
// Forward control
// State: [x, dx, theta, dtheta]
//        [distance travelled, speed, forward angle, rotational velocity]
const float A_F[4][4] = {{1,0.0932499806614936,-0.128465898713369,-0.00395403990363919},
                         {0,0.845687546747161,-3.09562497386320,-0.128465898713369},
                         {0,0.0655715718247256,2.72393023041216,0.152926756621594},
                         {0,1.58006908719785,41.7074774283773,2.72393023041216}};
const float B_F[4] = {0.00170886565531809,0.0390664438614782,-0.0166003979303103,-0.400017490429837};
const float C_F[4] = {1,1,1,1};
const float Q_F[4] = {0.5,0.5,2,1}; // State deviation weight LQR
const float V_F[4] = {0.1,0.1,0.1,0.1}; // Verify through measurements
const float R_F = 3; // Input weight LQR
float U_F = 0;

LQR LQR_F(A_F, B_F, Q_F, R_F);
Kalman KALMAN_F(A_F, B_F, C_F, V_F);
ColumnVector4 State_F;
ColumnVector4 Obs_State_F;
ColumnVector4 Des_State_F;

// Sideways control
// State: [phi, dphi, alpha, dalpha]
//        [Side angle, rotational velocity, flywheel angle, rotational velocity]
const float A_S[4][4] = {{1.41146607741256,0.113372087314826,0,-0.000255074418624809},
                               {8.75203510129462,1.41146607741256,0,-0.00560148085730519},
                               {0,0,1,0.111574942057396},
                               {0,0,0,1.24010372302915}};
const float B_S[4] = {0.00161439505458740,0.0354524104892734,-0.0732591269455416,-1.51964381664016};
const float C_S[4] = {};
const float Q_S[4] = {1,1,0.5,0.5}; // State deviation weight LQR
const float V_S[4] = {0.1,0.1,0.1,0.1}; // Verify through measurements
const float R_S = 20; // Input weight LQR
float U_S = 0;  

LQR LQR_S(A_S, B_S, Q_S, R_S);
Kalman KALMAN_S(A_S, B_S, C_S, V_S);
ColumnVector4 State_S;
ColumnVector4 Obs_State_S;
ColumnVector4 Des_State_S;

// ================================================================
// ===                        CONTROL                           ===
// ================================================================

bool detectStart() {
  // Pitch and roll inside start range
  if ((abs(Pitch) < (5 * PI / 180.0)) && (abs(Roll) < (5 * PI / 180))) {
    // Turn off LED
    digitalWrite(LED_PIN, LOW);
    delay(500);
    return true;
  }
  return false;
}

bool detectFall() {
  // Pitch and roll outside safety range
  if ((abs(Pitch) > (30 * PI / 180.0)) || (abs(Roll) > (20 * PI / 180.0))) {
    // Safety procedure
    // Stop motors
    driveMotor(0, M1A, M1B);
    driveMotor(0, M2A, M2B);
    // Turn on LED
    digitalWrite(LED_PIN, HIGH);
    return true;
  }
  return false;
}

void updateStates() {
  // Get IMU and Encoder data
  pollDMP();
  pollEncoders();
  // Update observations
  Obs_State_F.setElement(0, wheelEncPos * 0.04); // distance travelled
  Obs_State_F.setElement(1, wheelEncVel * 0.04); // speed
  Obs_State_F.setElement(2, -1 * Pitch); // forward angle
  Obs_State_F.setElement(3, PitchVel); // rotational velocity
  Obs_State_S.setElement(0, Roll); // side angle
  Obs_State_S.setElement(1, RollVel); // rotational velocity sideways
  Obs_State_S.setElement(2, flyEncPos); // flywheel angle
  Obs_State_S.setElement(3, flyEncVel); // rotational velocity flywheel
  // Use Kalman filter to determine velocities (or low pass filter)
  KALMAN_F.updateState(State_F, Obs_State_F, U_F);
  KALMAN_S.updateState(State_S, Obs_State_S, U_S);
  // DEBUG
  /*DPRINTSFN(10, " STATE 1:", wheelEncPos * 0.04, -6, 2);
  DPRINTSFN(10, " STATE 2:", wheelEncVel * 0.04, -6, 2);
  DPRINTSFN(10, " STATE 3:", -1 * Pitch, -6, 2);
  DPRINTSFN(10, " STATE 4:", PitchVel, -6, 5);
  DPRINTLN();*/
  DPRINTSFN(10, " Roll:", Roll, -6, 3);
  DPRINTSFN(10, " RollVel:", RollVel, -6, 3);
  DPRINTLN();
}

void computeInputs() {
  // LQR model for computing inputs
  int its_F = LQR_F.computeInput(State_F, Des_State_F, U_F);
  int its_S = LQR_S.computeInput(State_S, Des_State_S, U_S);
  // Constrain input to motor voltage (otherwise, Kalman filter won't be correct)
  U_F = constrain(U_F, -12.0, 12.0);
  U_S = constrain(U_S, -12.0, 12.0);
  // Debugging purposes
  DPRINTSFN(10, " INPUT_F:", U_F, -6, 2);
  DPRINTSFN(10, " INPUT_S:", U_S, -6, 2);
  DPRINTLN();
}

void applyControl() {
  // Apply calculated inputs to correct motors
  driveMotor(U_S, M1A, M1B); // Flywheel
  //driveMotor(U_F, M2A, M2B); // Wheel
}

// ================================================================
// ===                         SETUP                            ===
// ================================================================
void setup() {
  Serial.begin(115200);
  // Wait for Serial Monitor to be ready
  #ifdef DEBUG
    //while (!Serial); 
  #endif
  Serial.println(F("Setting up I2C..."));
  i2cSetup();
  Serial.println(F("Initialising MPU6050..."));
  MPU6050Connect();
  Serial.println(F("Setting up motor encoders..."));
  encoderSetup();
  Serial.println(F("Setting up motors..."));
  motorSetup();
  Serial.println(F("Testing motors in 2s..."));
  delay(2000);
  testMotors();
  Serial.println(F("Motor test completed..."));
  Serial.println(F("Setting up interrupt timers..."));
  timersSetup();
  
  pinMode(LED_PIN, OUTPUT);
  digitalWrite(LED_PIN, HIGH);
}

// ================================================================
// ===                          Loop                            ===
// ================================================================
void loop() {
  
  while (!detectStart()) {
    // Update IMU values
    pollDMP();
    delay(50);
  }
  
  while (!detectFall()) {
    // Check for control interrupt
    if (controlInterrupt) {
      // Turn update flag off
      controlInterrupt = false;
      // Update States
      updateStates();
      // Calculate control
      computeInputs();
      // Apply control
      applyControl();
    }
  }
}

// ================================================================
// ===                Debug Matrix/Vector Class                 ===
// ================================================================
// Put this in a unit test module or something
void debugMatVec() {
  // Initialize
  float matArr[4][4] {{19,7,16,2},{19,19,8,3},{10,8,5,19},{10,3,9,20}};
  float rowArr[4] {12,2,5,8};
  float colArr[4] {17,1,1,4};
  Matrix4 mat(matArr);
  RowVector4 rowvec(rowArr);
  ColumnVector4 colvec(colArr);
  
  // Multiplication
  float mat2Arr[4][4] {{674,400,458,403},{832,567,523,307},{582,319,420,519},{537,259,409,600}};
  float rowmat[4] {396,186,305,285};
  float matcol[4] {354,362,259,262};
  float vecvec[4][4] {{204,34,85,136},{12,2,5,8},{12,2,5,8},{48,8,20,32}};

  assert((mat * mat) == Matrix4(mat2Arr));
  assert((rowvec * mat) == RowVector4(rowmat));
  assert((mat * colvec) == ColumnVector4(matcol));
  assert((rowvec * colvec) == 243);
  assert((colvec * rowvec) == Matrix4(vecvec));
  assert(rowvec.T() == ColumnVector4(rowArr));
}

// handle diagnostic informations given by assertion and abort program execution:
void __assert(const char *__func, const char *__file, int __lineno, const char *__sexp) {
    // transmit diagnostic informations through serial link. 
    Serial.println(__func);
    Serial.println(__file);
    Serial.println(__lineno, DEC);
    Serial.println(__sexp);
    Serial.flush();
    // abort program execution.
    abort();
}

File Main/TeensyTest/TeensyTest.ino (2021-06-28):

/* ============================================
I2Cdev device library code is placed under the MIT license
Copyright (c) 2012 Jeff Rowberg

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
THE SOFTWARE IS PROVIDED "AS IS", WITHOUT WARRANTY OF ANY KIND, EXPRESS OR
IMPLIED, INCLUDING BUT NOT LIMITED TO THE WARRANTIES OF MERCHANTABILITY,
FITNESS FOR A PARTICULAR PURPOSE AND NONINFRINGEMENT. IN NO EVENT SHALL THE
AUTHORS OR COPYRIGHT HOLDERS BE LIABLE FOR ANY CLAIM, DAMAGES OR OTHER
LIABILITY, WHETHER IN AN ACTION OF CONTRACT, TORT OR OTHERWISE, ARISING FROM,
OUT OF OR IN CONNECTION WITH THE SOFTWARE OR THE USE OR OTHER DEALINGS IN
THE SOFTWARE.
===============================================
*/

// I2Cdev and MPU6050 must be installed as libraries, or else the .cpp/.h files
// for both classes must be in the include path of your project
#include "I2Cdev.h"
#include "MPU6050_6Axis_MotionApps20.h"
// Arduino Wire library is required if I2Cdev I2CDEV_ARDUINO_WIRE implementation
// is used in I2Cdev.h
#if I2CDEV_IMPLEMENTATION == I2CDEV_ARDUINO_WIRE
    #include "Wire.h"
#endif

// class default I2C address is 0x68
MPU6050 mpu;
//MPU6050 mpu(0x69); // <-- use for AD0 high

// DEBUG MODE
#define DEBUG

// Usefull macros
#define DPRINTSTIMER(t)    for (static unsigned long SpamTimer; (unsigned long)(millis() - SpamTimer) >= (t); SpamTimer = millis())
#define DPRINTSFN(StrSize,Name,...) {char S[StrSize];Serial.print("\t");Serial.print(Name);Serial.print(" "); Serial.print(dtostrf((float)__VA_ARGS__ ,S));} //StringSize,Name,Variable,Spaces,Percision
#define DPRINTLN(...)      Serial.println(__VA_ARGS__)

#define INTERRUPT_PIN 2 // All pins have interrupt capability on Teensy
#define LED_PIN 13 // Teensy 4.0 13

bool blinkState = false;

// MPU control/status vars
bool dmpReady = false;  // set true if DMP init was successful
uint8_t mpuIntStatus;   // holds actual interrupt status byte from MPU
uint8_t devStatus;      // return status after each device operation (0 = success, !0 = error)
uint16_t packetSize;    // expected DMP packet size (default is 42 bytes)
uint16_t fifoCount;     // count of all bytes currently in FIFO
uint8_t fifoBuffer[64]; // FIFO storage buffer

// Orientation/motion vars
Quaternion q;           // [w, x, y, z]         quaternion container
VectorInt16 aa;         // [x, y, z]            accel sensor measurements
VectorInt16 aaReal;     // [x, y, z]            gravity-free accel sensor measurements
VectorInt16 aaWorld;    // [x, y, z]            world-frame accel sensor measurements
VectorFloat gravity;    // [x, y, z]            gravity vector
float euler[3];         // [psi, theta, phi]    Euler angle container
float ypr[3];           // [yaw, pitch, roll]   yaw/pitch/roll container and gravity vector

// packet structure for InvenSense teapot demo
// uint8_t teapotPacket[14] = { '$', 0x02, 0,0, 0,0, 0,0, 0,0, 0x00, 0x00, '\r', '\n' };

// ================================================================
// ===               INTERRUPT DETECTION ROUTINE                ===
// ================================================================

volatile bool mpuInterrupt = false;     // indicates whether MPU interrupt pin has gone high

// Triggered by IMU with interrupt pin
void dmpDataReady() {
    mpuInterrupt = true;
}

// ================================================================
// ===                      INITIAL SETUP                       ===
// ================================================================

void setup() {
    // Join I2C bus (I2Cdev library doesn't do this automatically)
    #if I2CDEV_IMPLEMENTATION == I2CDEV_ARDUINO_WIRE
        Wire.begin();
        Wire.setClock(400000); // 400kHz I2C clock. Comment this line if having compilation difficulties
    #elif I2CDEV_IMPLEMENTATION == I2CDEV_BUILTIN_FASTWIRE
        Fastwire::setup(400, true);
    #endif

    // Initialize serial communication
    Serial.begin(115200);
    while (!Serial); // wait for Leonardo enumeration, others continue immediately

    // NOTE: 8MHz or slower host processors, like the Teensy @ 3.3V or Arduino
    // Pro Mini running at 3.3V, cannot handle this baud rate reliably due to
    // the baud timing being too misaligned with processor ticks. You must use
    // 38400 or slower in these cases, or use some kind of external separate
    // crystal solution for the UART timer.

    // Initialize device
    Serial.println(F("Initializing I2C devices..."));
    mpu.initialize();
    pinMode(INTERRUPT_PIN, INPUT);

    // Verify connection
    Serial.println(F("Testing device connections..."));
    Serial.println(mpu.testConnection() ? F("MPU6050 connection successful") : F("MPU6050 connection failed"));

    // Wait for user input to start => maybe use for debugging?
    /* Serial.println(F("\nSend any character to begin DMP programming and demo: "));
    while (Serial.available() && Serial.read()); // empty buffer
    while (!Serial.available());                 // wait for data
    while (Serial.available() && Serial.read()); // empty buffer again
    */
    
    // Load and configure the DMP
    Serial.println(F("Initializing DMP..."));
    devStatus = mpu.dmpInitialize();

    // IMU offsets
    int MPUOffsets[6] = {-987,-1278,1197,-14,73,97};
    
    // Assign offsets
    mpu.setXAccelOffset(MPUOffsets[0]);
    mpu.setYAccelOffset(MPUOffsets[1]);
    mpu.setZAccelOffset(MPUOffsets[2]);
    mpu.setXGyroOffset(MPUOffsets[3]);
    mpu.setYGyroOffset(MPUOffsets[4]);
    mpu.setZGyroOffset(MPUOffsets[5]);

    // Make sure it worked (returns 0 if so)
    if (devStatus == 0) {
        // Calibration Time: generate offsets and calibrate our MPU6050
        mpu.CalibrateAccel(6);
        mpu.CalibrateGyro(6);
        mpu.PrintActiveOffsets();
        
        // Turn on the DMP, now that it's ready
        Serial.println(F("Enabling DMP..."));
        mpu.setDMPEnabled(true);

        // e-Enable Arduino interrupt detection
        Serial.print(F("Enabling interrupt detection (Arduino external interrupt "));
        Serial.print(digitalPinToInterrupt(INTERRUPT_PIN));
        Serial.println(F(")..."));
        attachInterrupt(digitalPinToInterrupt(INTERRUPT_PIN), dmpDataReady, RISING);
        mpuIntStatus = mpu.getIntStatus();

        // Set our DMP Ready flag so the main loop() function knows it's okay to use it
        Serial.println(F("DMP ready! Waiting for first interrupt..."));
        dmpReady = true;

        // Get expected DMP packet size for later comparison
        packetSize = mpu.dmpGetFIFOPacketSize();
    } else {
        // ERROR!
        // 1 = initial memory load failed
        // 2 = DMP configuration updates failed
        // (if it's going to break, usually the code will be 1)
        Serial.print(F("DMP Initialization failed (code "));
        Serial.print(devStatus);
        Serial.println(F(")"));
    }

    // configure LED for output
    pinMode(LED_PIN, OUTPUT);
}
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

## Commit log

2021-06-27 Updated flywheel design and addition of NOTES.md file
    [626_2Z.sldasm, Battery.SLDPRT, Contra.SLDPRT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]
2021-06-28 Updated calibration values
2021-06-30 Updated mass properties in model and simulation software
    [OneWheel.SLDASM, Vliegwiel.SLDPRT, fath_4din439bm8e.SLDPRT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]
2021-08-16 Added encoder support
2021-08-16 Updated circuit files
    [copper_bottom.gbr, copper_top.gbr, drill_1_16.xln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]
2021-08-17 Motor control methods, updated gitignore for stl files, cleanup of code
    [OneWheel.SLDASM]
2021-08-17 Removal of unintended STL file
    [Velg.STL]
2021-08-23 Kalman filter push for remote work
2021-08-29 Update project structure to include edited libraries
    [Battery.SLDPRT, Contra.SLDPRT, OneWheel.SLDASM]
